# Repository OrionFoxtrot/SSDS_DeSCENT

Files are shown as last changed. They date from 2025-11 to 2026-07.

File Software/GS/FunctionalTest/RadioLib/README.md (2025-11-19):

# RadioLib   

### _One radio library to rule them all!_

## Universal wireless communication library for embedded devices

RadioLib allows its users to integrate all sorts of different wireless communication modules, protocols and even digital modes into a single consistent system.
Want to add a Bluetooth interface to your LoRa network? Sure thing! Do you just want to go really old-school and play around with radio teletype, slow-scan TV, or even Hellschreiber using nothing but a cheap radio module? Why not!

RadioLib natively supports Arduino, but can run in non-Arduino environments as well! See [this Wiki page](https://github.com/jgromes/RadioLib/wiki/Porting-to-non-Arduino-Platforms) and [examples/NonArduino](https://github.com/jgromes/RadioLib/tree/master/examples/NonArduino).

RadioLib was originally created as a driver for [__RadioShield__](https://github.com/jgromes/RadioShield), but it can be used to control as many different wireless modules as you like - or at least as many as your microcontroller can handle!

### Quick links:
* [__Wiki__](https://github.com/jgromes/RadioLib/wiki) - contains useful general information on using this library
* [__FAQ__](https://github.com/jgromes/RadioLib/wiki/Frequently-Asked-Questions) - frequently asked questions, and answers
* [__API Reference__](https://jgromes.github.io/RadioLib) - full API reference, automatically generated from the source code
* [__Status Code Decoder__](https://radiolib-org.github.io/status_decoder/decode.html) - decoder for status codes returned by RadioLib methods
* [__Debug Log Decoder__](https://radiolib-org.github.io/debug_decoder/decode.html) - decoder for RadioLib SPI debug logs

### Supported modules:
* __CC1101__ FSK radio module
* __LLCC68__ LoRa module
* __LR11x0__ series LoRa/GFSK modules (LR1110, LR1120, LR1121)
* __nRF24L01__ 2.4 GHz module
* __RF69__ FSK/OOK radio module
* __RFM2x__ series FSK modules (RFM22, RFM23)
* __RFM9x__ series LoRa modules (RFM95, RFM96, RFM97, RFM98)
* __Si443x__ series FSK modules (Si4430, Si4431, Si4432)
* __STM32WL__ integrated microcontroller/LoRa module
* __SX126x__ series LoRa modules (SX1261, SX1262, SX1268)
* __SX127x__ series LoRa modules (SX1272, SX1273, SX1276, SX1277, SX1278, SX1279)
* __SX128x__ series LoRa/GFSK/BLE/FLRC modules (SX1280, SX1281, SX1282)
* __SX123x__ FSK/OOK radio modules (SX1231, SX1233)

### Supported protocols and digital modes:
* [__AX.25__](https://www.sigidwiki.com/wiki/PACKET) using 2-FSK or AFSK for modules:  
SX127x, RFM9x, SX126x, RF69, SX1231, CC1101, RFM2x, Si443x, LR11x0 and SX128x
* [__RTTY__](https://www.sigidwiki.com/wiki/RTTY) using 2-FSK or AFSK for modules:  
SX127x, RFM9x, SX126x, RF69, SX1231, CC1101, nRF24L01, RFM2x, Si443x, LR11x0 and SX128x
* [__Morse Code__](https://www.sigidwiki.com/wiki/Morse_Code_(CW)) using 2-FSK or AFSK for modules:  
SX127x, RFM9x, SX126x, RF69, SX1231, CC1101, nRF24L01, RFM2x, Si443x, LR11x0 and SX128x
* [__SSTV__](https://www.sigidwiki.com/wiki/SSTV) using 2-FSK or AFSK for modules:  
SX127x, RFM9x, SX126x, RF69, SX1231, CC1101, RFM2x and Si443x
* [__Hellschreiber__](https://www.sigidwiki.com/wiki/Hellschreiber) using 2-FSK or AFSK for modules:  
SX127x, RFM9x, SX126x, RF69, SX1231, CC1101, nRF24L01, RFM2x, Si443x, LR11x0 and SX128x
* [__APRS__](https://www.sigidwiki.com/wiki/APRS) using AFSK for modules:  
SX127x, RFM9x, SX126x, RF69, SX1231, CC1101, nRF24L01, RFM2x, Si443x and SX128x
* [__POCSAG__](https://www.sigidwiki.com/wiki/POCSAG) using 2-FSK for modules:  
SX127x, RFM9x, RF69, SX1231, CC1101, nRF24L01, RFM2x and Si443x
* [__LoRaWAN__](https://lora-alliance.org/) using LoRa and FSK for modules:  
SX127x, RFM9x, SX126x, LR11x0 and SX128x
  * Supports Class A and C (and Multicast over C).
  * Pre-certified for Class A.
  * See the [wiki](https://github.com/jgromes/RadioLib/wiki/LoRaWAN) and [notes](https://github.com/jgromes/RadioLib/blob/master/examples/LoRaWAN/LoRaWAN_Starter/notes.md) for more information.

### Supported Arduino platforms:
* __Arduino__  
  * [__AVR__](https://github.com/arduino/ArduinoCore-avr) - Arduino Uno, Mega, Leonardo, Pro Mini, Nano etc.
    * NOTE: Arduino boards based on ATmega328 (Uno, Pro Mini, Nano etc.) and smaller are NOT recommended. This is because the ATmega328 MCU is very constrained in terms of program and memory size, so the library will end up taking most of the space available. 
  * [__mbed__](https://github.com/arduino/ArduinoCore-mbed) - Arduino Nano 33 BLE and Arduino Portenta H7
  * [__megaAVR__](https://github.com/arduino/ArduinoCore-megaavr) - Arduino Uno WiFi Rev.2 and Nano Every
  * [__SAM__](https://github.com/arduino/ArduinoCore-sam) - Arduino Due
  * [__SAMD__](https://github.com/arduino/ArduinoCore-samd) - Arduino Zero, MKR boards, M0 Pro etc.
  * [__Renesas__](https://github.com/arduino/ArduinoCore-renesas) - Arduino Uno R4

* __Adafruit__
  * [__SAMD__](https://github.com/adafruit/ArduinoCore-samd) - Adafruit Feather M0 and M4 boards (Feather, Metro, Gemma, Trinket etc.)
  * [__nRF52__](https://github.com/adafruit/Adafruit_nRF52_Arduino) - Adafruit Feather nRF528x, Bluefruit and CLUE

* __Espressif__
  * [__ESP32__](https://github.com/espressif/arduino-esp32) - ESP32-based boards
  * [__ESP8266__](https://github.com/esp8266/Arduino) - ESP8266-based boards

* __Intel__
  * [__Curie__](https://github.com/arduino/ArduinoCore-arc32) - Arduino 101

* __SparkFun__
  * [__Apollo3__](https://github.com/sparkfun/Arduino_Apollo3) - Sparkfun Artemis Redboard

* __ST Microelectronics__
  * [__STM32__ (official core)](https://github.com/stm32duino/Arduino_Core_STM32) - STM32 Nucleo, Discovery, Maple, BluePill, BlackPill etc.
  * [__STM32__ (unofficial core)](https://github.com/rogerclarkmelbourne/Arduino_STM32) - STM32F1 and STM32F4-based boards

* __MCUdude__
  * [__MegaCoreX__](https://github.com/MCUdude/MegaCoreX) - megaAVR-0 series (ATmega4809, ATmega3209 etc.)
  * [__MegaCore__](https://github.com/MCUdude/MegaCore) - AVR (ATmega1281, ATmega640 etc.)

* __Raspberry Pi__
  * [__RP2040__ (official core)](https://github.com/arduino/ArduinoCore-mbed) - Raspberry Pi Pico and Arduino Nano RP2040 Connect
  * [__RP2040__ (unofficial core)](https://github.com/earlephilhower/arduino-pico) - Raspberry Pi Pico/RP2040-based boards
  * [__Raspberry Pi__](https://github.com/me-no-dev/RasPiArduino) - Arduino framework for RaspberryPI

* __Heltec__
  * [__CubeCell__](https://github.com/HelTecAutomation/CubeCell-Arduino) - ASR650X series (CubeCell-Board, CubeCell-Capsule, CubeCell-Module etc.)

* __PJRC__
  * [__Teensy__](https://github.com/PaulStoffregen/cores) - Teensy 2.x, 3.x and 4.x boards

* __Silicon Labs__
  * [__EFR32__](https://github.com/SiliconLabs/arduino) - Silicon Labs xG24, xG27 and other boards

The list above is by no means exhaustive - RadioLib code is independent of the used platform! Compilation of all examples is tested for all platforms officially supported prior to releasing new version. In addition, RadioLib includes an internal hardware abstraction layer, which allows it to be easily ported even to non-Arduino environments.

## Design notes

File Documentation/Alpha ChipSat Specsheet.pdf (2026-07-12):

# Flight-proven LEO ChipSat

## Designed for free-flying light sails (Alpha CubeSat mission)

## Applications

### - Low power, long range communications - Remote sensing / distributed sensing - Short-duration multi-day LEO operation - Atmospheric or ground-based sensing - Telemetry for lightweight solar/laser sails

### Dimensions: 58mm x 58mm x 3mm | Mass: 6g

## Capabilities Summary

Power: Wireless operation via 780mW PV (one-sided); Potential modifications: dual-sided solar or battery-only Processing: 16MHz CPU speed; 32KB Flash, 2KB SRAM; Potential modification: external flash memory

## Comms: Semtech SX1276; +20dBm TX; 70cm Band; LoRa, (G)FSK, (G)MSK, and OOK

Position/Attitude determination: GNSS Receiver + 9-DOF IMU (accelerometer, gyroscope, magnetometer)

## Environmental Sensing: Temperature + 3-DOF magnetometer from IMU Structure: Thin flexible polyimide (Kapton) PCB

## Survivability

## Vacuum ☑ | Launch loads/vibration ☑ | Radiation* ⮽ | Terminal-velocity ground impact ☑

Operating temperature: -40°C – +85°C (additional limitations if modified to include energy storage)
*No radiation shielding / rad-hard avionics –recommended for short-term missions w/ large quantities of ChipSats

## Additional Specifications

`

MCU | ATmega328p-AU
I/O Pins: | UART x1, I2C x1, SPI x1, 10-bit ADC x6, GPIO x8 | Sleep current: | 4.4 µA
Clock Speed: | 16MHz | Flash Memory: | 32KB | SRAM: | 2KB | EEPROM: | 1KB
Sensors | STS21 Temperature Sensor | LSM9DS1 9-DOF IMU
Temp | Accel | Gyro | Mag
Resolution: | 0.08°C | 0.732 mg | 0.875 dps | 0.014 µT
Range: | -40° - 125°C | ± 16g | ± 245 dps | ±400 µT
GPS | SkyTraq Orion B16-01; L1 GPS/Galileo/GLONASS/BeiDou/QZSS; Space-rated
Accuracy: | Position: | 2m | Velocity: | 0.1m/s | Time: | 5ns | TTFF: | 1 min
Power | L6920 regulator IC + 780mW GaAs PV | No energy storage onboard
Lifespan | Indefinite operation under solar illumination (dependent on sun-orientation)
Comms | SX1276 (built into HopeRF RFM96W); also capable of (G)FSK, (G)MSK, OOK
Freq: | 433MHz | BW: | 7.8 - 500KHz | TX PWR: | +20dBm | Modulation: | LoRa
Approx. Range: | (w/ below receiver equipment) | 50km | LEO | GEO | Cislunar
Estimated LoRa Data rate (bps): | | Low-gain omni | 488 bps | 146 bps | X | X
| | High-gain Yagi | 3.5 kbps | 488 bps | 45 bps | X
| | Large parabolic dish | 22 kbps | 3.5 kbps | 146 bps | 11 bps

## ChipSat layout

### ChipSat architecture

For more information:
✉ mp336@cornell.edu spacecraftresearch.com

Est. cost (per ChipSat):

## $1300 USD (Orbital) / $200 USD (Terrestrial)

# ChipSat V5 (2022-2025)

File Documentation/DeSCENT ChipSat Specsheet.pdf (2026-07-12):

## Compact ChipSat with solar battery charging

## Designed for suborbital rocket deployment and atmospheric data collection (DeSCENT mission)

## Applications

## - Low power, long range communications - Remote sensing / distributed sensing - Short-duration multi-day LEO operation - Atmospheric or ground-based sensing

## Dimensions: 60mm x 50mm x 4.5mm | Mass: 20g

## Capabilities Summary

Power: Wireless self-sustaining operation via dual 300mW PV (one per side) + 300mAh LiPo battery Processing: 32-bit ARM Cortex-M4; 48MHz; 256KB Flash, 65KB SRAM; 2MB external flash memory

## Comms: Semtech SX126x; +22dBm TX; 915MHz ISM Band; LoRa, (G)FSK, (G)MSK, and BPSK

Position/Attitude determination: GNSS Receiver + 9-DOF IMU (accelerometer, gyroscope, magnetometer) Environmental Sensing: Temperature, pressure, and humidity sensors; 3-DOF magnetometer from IMU

## Survivability

## Vacuum ☑ | Launch loads/vibration ☑ | Radiation* ⮽ | Terminal-velocity ground impact ☑

Operating temperature: -10°C – +60°C with LiPo battery | -40°C – +85°C with solar-only configuration
*No radiation shielding / rad-hard avionics –recommended for short-term missions w/ large quantities of ChipSats

## Additional Specifications

MCU | Seeed Studio Wio-E5 (STM32WLE5 32-bit ARM Cortex M4) + W25Q16 Ext Flash
I/O Pins: | UART x3, I2C x1, SPI x1, 12-bit ADC x1, GPIO x6 | Sleep current: | 2.1 µA
Clock Speed: | 48MHz | Flash Memory: | 256KB | SRAM: | 65KB | Ext. Flash: | 2MB
Sensors | BME280 Environmental | BNO085 9-DOF IMU
Temp | Pressure | Humidity | Accel | Gyro | Mag
Accuracy: | 1°C | 1.0 hPa | 3% RH | 0.3m/s² | 3.1 dps | 1.4 µT
Range: | -40°-85°C | 300-1100 hPa | 0-100% | ± 8g | ± 2000 dps | ±800 µT
GPS | u-blox MAX M10S; L1 GPS/Galileo/GLONASS/BeiDou; NOTE: CoCom Limits
Accuracy: | 2m | TTFF: | 2 min | Max alt: | 80km | Max vel: | 500m/s
Power | BQ25570 regulator IC + 300mAh LiPo Batt + 300mW GaAs PV
Batt. Life: | 10hr battery-only operation w/ frequent radio TX | Indefinite w/ solar charging
Comms | SX126x (built into Wio-E5 MCU); also capable of (G)FSK, (G)MSK, and BPSK
Freq: | 915MHz | BW: | 62.5 - 500KHz | TX PWR: | +22dBm | Modulation: | LoRa
Approx. Range: | (w/ below receiver equipment) | 50km | LEO | GEO | Cislunar
Estimated LoRa Data rate (bps): *requires hardware change | | Low-gain omni | 488 bps | 91 bps | X | X
| | High-gain Yagi | 3.5 kbps | 268 bps | 36 bps* | X
| | Large parabolic dish | 22 kbps | 1.9 kbps | 91 bps | 11 bps*

# ChipSat V6 (2023-2026)

## ChipSat layout

## ChipSat architecture

For more information:

### ✉ mp336@cornell.edu spacecraftresearch.com

Est. cost:

## $200 USD

per ChipSat

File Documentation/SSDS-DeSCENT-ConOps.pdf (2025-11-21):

# Concept of Operations (ConOps) – DeSCENT Mission

## 1 1. Mission Overview

The Demonstration of Suborbital ChipSats Ejected from New Shepard Test Flight (DeSCENT) is a Cornell SSDS mission in collaboration with Johns Hopkins APL.

The mission will deploy 100 ChipSats from a Blue Origin New Shepard suborbital launch vehicle at ~100 km altitude.

## 1.1 Primary objectives:

Goal 1 The mission shall collect in-situ sensor data from a distributed fleet of chipsats.

Goal 1.1 The mission shall collect data that demonstrates the potential of chipsats for atmospheric science. [Goal 1]

Goal 2 The mission shall characterize the free-fall dispersion dynamics and the landing ellipse of a chipsat fleet.

## 2 Mission Phases

## 2.1 Pre-Launch Integration

The DeSCENT payload consists of a spring-loaded deployer containing 100 ChipSats, integrated alongside other experiments within the APL JANUS platform for the New Shepard propulsion Module (PM).

ChipSats remain powered off inside the deployer until ejection, per safety requirements.

Payload is mounted within an AxBxC mm envelope, inverted relative to vehicle axes.

## 2.2 Launch & Ascent

New Shepard PM launches vertically from Blue Origin’s West Texas Launch Site.

The BE-3 engine burns for ~2.5 minutes, propelling the vehicle and payload stack above 100 km altitude.

ChipSats remain stowed; environmental loads are verified against payload specifications.

## 2.3 Apogee & Deployment

At apogee (~100 km, ~T+3 min), a burn-wire mechanism triggers deployer springs, releasing ChipSats at ~0.2–0.4 m/s relative velocity.

Doors hinge open, ejecting ChipSats into free space.

Deployment is vertical relative to launch orientation, ensuring controlled dispersion.

## 2.4 Free-Fall Descent

Each ChipSat (~20 g, <50×50×4 mm) enters a ballistic free-fall trajectory, reaching terminal velocities between ~110–220 m/s.

Onboard sensors (BME280, BNO085 IMU, GNSS) continuously log data.

Communications strategy:

- Low-density, real-time telemetry sent to ground station.
- High-density data stored in onboard flash retrievable upon recovery.

## 2.5 Impact & Recovery

ChipSats are designed to survive terminal impact due to their low mass and high structural frequencies.

GNSS beacons and LoRa transmissions support localization.

Ground recovery teams search the landing ellipse to collect ChipSats.

## 2.6 Post-Mission Analysis

Recovered ChipSats provide stored high-fidelity datasets.

Combined telemetry and flash data validate free-fall models, atmospheric measurements, and swarm dispersion behavior.

Results inform future ChipSat swarms for atmospheric entry on Earth or other planetary bodies.

## 3 Key Systems

Deployer: Aluminum structure with spring-loaded ejection bars and burn-wire trigger.

ChipSat Command and Data Handling: MCU/LoRa IC, Environmental sensors (BME280), IMU (BNO085), GNSS, Flash storage.

ChipSat Communications: LoRa at 915 MHz ISM band, asynchronous chirp spread spectrum modulation.

ChipSat Power: Solar and 350 mAh LiPo, low-duty cycle operation.

Integration Platform: APL’s JANUS system, providing power control, data monitoring, and environmental characterization.

## 4 Operational Constraints

Must meet Blue Origin payload integration requirements: mechanical envelope, EMI/EMC, vibration, and thermal testing.

Deployer must pose no risk to launch vehicle, other payloads, or personnel.

RF transmissions must not interfere with New Shepard telemetry.

Recovery probability and data survival are mission-critical success metrics.

## 5 Success Criteria (MIS Requirements)

MIS 1 One hundred chipsats shall be deployed from the New Shepard suborbital launch vehicle at approximately 100 km apogee.

MIS 2 The chipsat sensor data shall be collected from chipsat descent trajectories and landing positions.

MIS 2.1 The collected chipsat data shall contain in-situ atmospheric sensor data and measurements of chipsat free-fall kinematics. [MIS 2]

MIS 3 Two percent of chipsats shall survive terminal velocity impact with the ground.

MIS 4 X percent of chipsats shall be recovered after landing.

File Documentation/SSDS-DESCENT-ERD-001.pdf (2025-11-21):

Effective Date: September 9th, 2025 Revision: 0

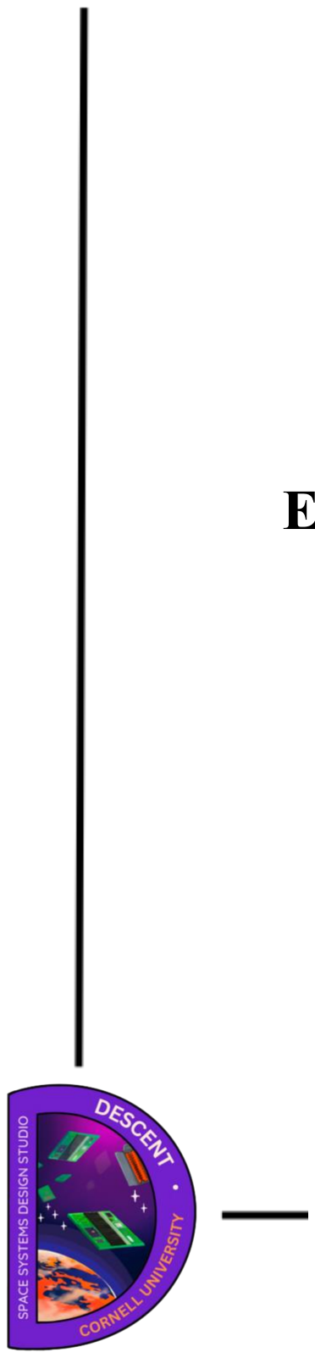
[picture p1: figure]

Check the DESCENT Box Folder at this URL (https://cornell.app.box.com/folder/213553157379?s=2hq835s9t41mr3z1efjbw8ddljec1i8f) to verify that this is the correct version prior to use.

## DESCENT SSDS-DESCENT-ERD-001

# DESCENT Engineering Requirements Document (ERD)

School of Mechanical & Aerospace Engineering Ithaca, New York

DESCENT Engineering Requirements Document (ERD) | SSDS-DESCENT-ERD-001
| Revision: 0

## DESCENT Engineering Requirements Document (ERD)

DESCENT Electronic Signature Page

Prepared By:

Mark Lohatepanont, Josh Umansky-Castro, Richard Zheng, Arthur Chadwick

Approved By:

__________________
____________________________________________

School of Mechanical & Aerospace Engineering Ithaca, New York

Revision: 0

## Preface

This is the Engineering Requirements Document (ERD) to be shared with relevant stakeholders on the DESCENT project. The ERD shows the requirements necessary for the mission, safety, deployer, chipsat, power, communications, command and data handling, mechanical, and environmental requirements.

Any questions should be addressed to:

Mark Lohatepanont
Cornell University PhD Student DESCENT project
ml2828@cornell.edu
Ithaca, NY 14850

Revision: 0

## Change History Log

Revision | Effective Date | Description of Changes | Sections Affected
0 | Sept. 9th, 2025 | Document formatting created based on NASA example[7] (https://www.nesdis.noaa.gov/s3/2022-03/474-00002-01_JPSS-CIS-ICD-Vol-I-_External_0124E.pdf) . Table of Contents outline created. Initial requirements transcribed from DESCENT requirements meeting. | All

Revision: 0

Revision: 0

### 0 What is an ERD?

An Engineering Requirements Document (ERD) is a collection of information that shares the “shall” statements, or the requirements, of a project. Engineers use these requirements to determine the scope of the design. An ERD may take other forms as well. Some examples of a technical requirements document used by NASA are a System Requirements Document (SRD), Project Requirements Document (PRD), Interface Requirements Document (IRD), and a Software Requirements Specification (SRS)[1] (https://www.nasa.gov/reference/4-2-technical-requirements-definition/)

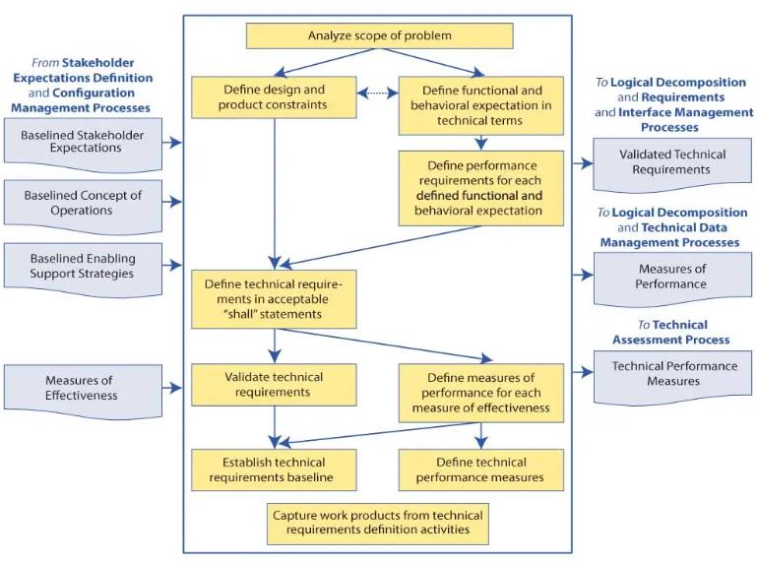
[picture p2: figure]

Figure: Technical Requirements Definition Process[1] (https://www.nasa.gov/reference/4-2-technical-requirements-definition/) .

Defining requirements connects the vision of the product or mission between stakeholders like the project managers, engineers, and customers; on the left side of the diagram above, we see those inputs mentioned. In the middle section, it outlines important actions in the process like defining constraints, functional vs performance requirements, and validation techniques. A requirement is as good as its applicability and validity. Measures of Performance (MOPs) and Technical Performance Measures (TPMs) are the measurable numbers in the requirements[1] (https://www.nasa.gov/reference/4-2-technical-requirements-definition/)

Revision: 0

### 0.1 Acronyms

APL | Applied Physics Laboratory
ADCS | Attitude Dynamics & Control Subsystem / Attitude Control System
CDH | Command and Data Handling
CONOPs | Concept of Operations
DPLY | Deployer
ERD | Engineering Requirements Document
ESD | Electrostatic Discharge
FCC | Federal Communications Commission
FMEA | Failure Modes & Effects Analysis
FMSA | Fault Management & System Autonomy
GPS | Global Positioning System
I&T | Integration & Test
INT | Integration
LV / LVA | Launch Vehicle
MIS | Mission
MIL-STD | Military Standard
MPP | Maximum Power Point
NASA | National Aeronautics Space Administration
NIR | Near Infrared Light
NTSS | NASA Technical Standards System
NTSP | NASA Technical Standards Program
OCE | Office of the NASA Chief Engineer
PCB | Printed Circuit Board
PLD | Payload
PWR | Power Subsystem / Power System / Electrical Power System
RF | Radio Frequency
SE | Space Environment
SSDS | Space Systems Design Studio
T&C | Telemetry & Command / Command & Data Handling
TBC | To Be Confirmed
TBD | To Be Determined
TCS | Thermal Control Subsystem / Thermal System
TPM | Technical Performance Measure
TRL | Technical Readiness Level
TTFF | Time to First Fix
FM | Fault Management

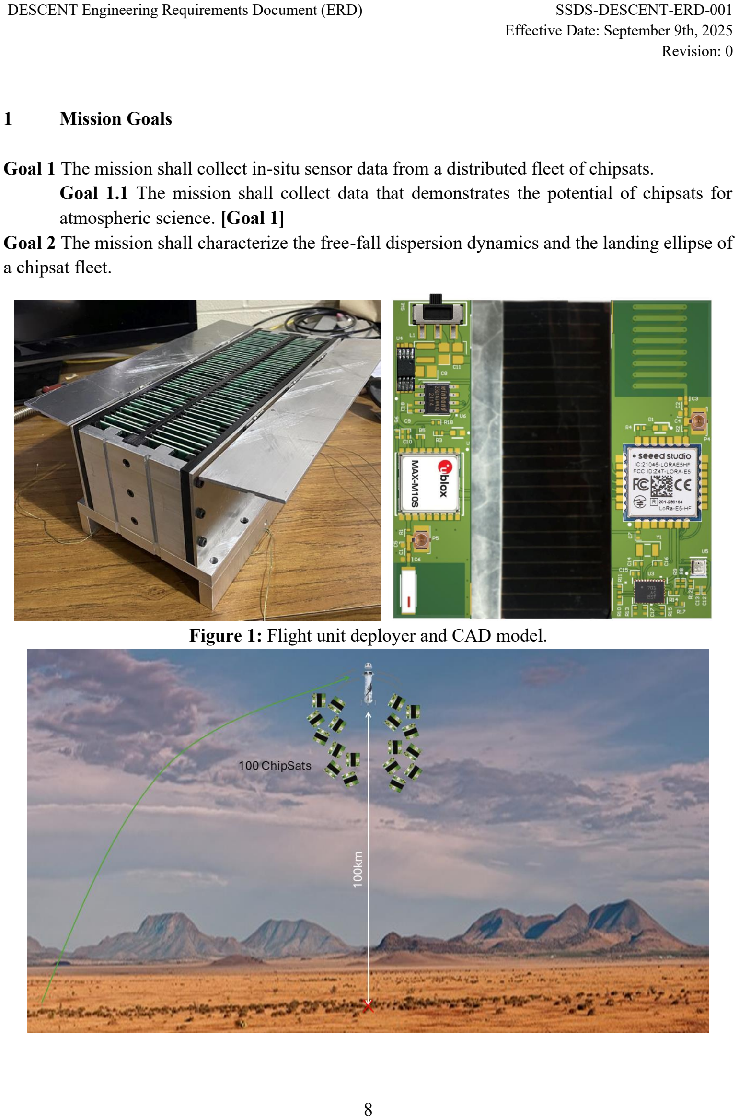
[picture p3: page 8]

Revision: 0

### 1 Mission Goals

Goal 1 The mission shall collect in-situ sensor data from a distributed fleet of chipsats.
Goal 1.1 The mission shall collect data that demonstrates the potential of chipsats for atmospheric science. [Goal 1]
Goal 2 The mission shall characterize the free-fall dispersion dynamics and the landing ellipse of a chipsat fleet.

Figure 1: Flight unit deployer and CAD model.

Revision: 0

Figure 2: Demonstration of Suborbital ChipSats Ejected from New Shepard Test Flight (DeSCENT).

Revision: 0

### 2 Mission-Level Requirements

MIS 1 One hundred chipsats shall be deployed from the New Shepard suborbital launch vehicle at approximately 100 km apogee.
MIS 2 The chipsat sensor data shall be collected from chipsat descent trajectories and landing positions.
MIS 2.1 The collected chipsat data shall contain in-situ atmospheric sensor data and measurements of chipsat free-fall kinematics. [MIS 2]
MIS 3 Two percent of chipsats shall survive terminal velocity impact with the ground.
MIS 4 X percent of chipsats shall be recovered after landing.

### 3 Safety Requirements

FM 1 The chipsat shall be powered off when stowed in the deployer. [MIS 4]
FM 2 The chipsat shall have X mAh capacity. [MIS 4]
FM 3 The chipsat RF transmissions shall not interfere with the New Shepard launch vehicle. [MIS 4]
FM 3.1 The chipsat RF transmit power (TX) and frequency shall not interfere with the New Shepard launch vehicle. [FM 3]
FM 4 The chipsat shall weigh < X g. [MIS 4]
FM 5 The mechanical deployer shall remain in-tact and attached to the rocket. [MIS 4]
FM 6 The burn-wire shall not disrupt operations. [MIS 4]
FM 7 The chipsat deployer shall cause no harm to the vehicle, payloads, or personnel. [Blue Origin, APL]
FM 7.1 The chipsat deployer shall cause no harm to Blue Origin’s Propulsion Module. [FM 7]
FM 7.2 The chipsat deployer shall cause no harm to Blue Origin’s Crew Capsule. [FM 7] The chipsat deployer shall cause no harm to John Hopkins’ APL JANUS payload. [FM 7] FM 7.3 The chipsat deployer shall cause no harm to other payloads. [FM 7]
FM 7.4 The chipsat deployer shall cause no harm to Blue Origin personnel. [FM 7]

### 4 Deployment Requirements

DPLY 1 The deployer shall automatically deploy at apogee. [MIS 2]
DPLY 1.1 The deployer shall deploy during APL pulsed signal. [DPLY 1] DPLY 1.2 The deployer shall deploy between two to four minutes. [DPLY 1] DPLY 2 The deployer shall deploy vertically from NS Launch. [MIS 2]

Revision: 0

DPLY 3 The deployer shall deploy chipsats at 0.2 to 0.4 m/s. [MIS 4]
DPLY 4 The deployer shall interface using a MIL-STD D-Sub connector to APL’s JANUS payload. [MIS 4]
DPLY 5 The deployer shall be bounded by X volume. [MIS 4]
DPLY 6 The deployer shall weigh less than 50 lbs (10 kg).
DPLY 7 The deployer shall survive the launch and launch environment. DPLY 8 The deployer shall deploy at -46 degrees Celsius.
DPLY 9 The deployer shall house and deploy 100 chipsats.
DPLY 10 The deployer shall be mounted to the APL JANUS plate.
DPLY 11 The deployer shall adhere to the Blue Origin Propulsion Module User’s Guide.
DPLY 12 The deployer slots shall house chipsats of size | X | m, | X | m, | X | m.
DPLY 13 The deployer shall have the capability to be stowed for 3 months.

### 5 Chipsat Requirements

### 5.1 Power Requirements

PWR 1 The chipsat shall remain off when stowed in the deployer and turn on upon deployment PWR 1.1 The chipsat shall have a snap action lever switch to activate the circuit upon deployment. [PWR 1, MECH X]
PWR 1.2 The chipsat batteries shall be fully charged when stowed before launch.
PWR 2 The chipsat shall remain on during descent and recovery. [MIS 1, MIS 2]
PWR 2.1 The chipsat shall remain powered on via solar during extended recovery. [PWR 2]
PWR 2.1.1 The chipsat maximum power draw shall not continuously, for 1 hour, bleed MPP of solar cell @ 300 mA @ 1.1V. [PWR 2.1]
PWR 2.1.2 The chipsat solar panel shall be able to recharge the battery. [PWR 2.1] PWR 2.2 The chipsat battery capacity shall be sufficient for X hours of operation. [PWR 2]
PWR 2.3 The chipsat battery shall be used to store energy during descent and short term recovery. [PWR 2]

### 5.2 Communications Requirements

COMMS 1 The chipsat shall communicate across descent and recovery.
COMMS 1.1 The chipsat ground communications link shall be maintained across the longest distance at Propulsion Module apogee. [COMMS 1]
COMMS 2 The chipsat TX power shall remain within maximum power draw of the power source.

Revision: 0

COMMS 3 The chipsat communications shall be maintained via commercially available, low power, and long range chips.
COMMS 3.1 The chipsat communications shall use a 915 mHz Lora chip. [COMMS 3] COMMS 4 The chipsat communications shall begin when each chipsat leaves the deployer. COMMS 5 The chipsats shall stop transmitting on command. [MIS 4]
COMMS 6 The chipsat communications shall transmit at 0.1 Hz during the descent phase.
COMMS 7 The chipsat shall transmit at | X | Hz (once every 10-20 sec) when in ground recovery
phase.
COMMS 8 The chipsat communications antenna shall fit within the mechanical envelope. [MECH 3.X]
COMMS 8.1 The chipsat communications antenna shall be a helical PCB.

### 5.3 Command & Data Handling

CDH 1 Data acquisition shall start after the chipsats leave the deployer.
CDH 2 All sensors shall sample at > 1 Hz during descent.
CDH 3 The chipsat shall collect internal and external data.
CDH 3.1 The chipsat shall collect humidity, temperature, pressure. [CDH 3]
CDH 3.2 The chipsat shall collect linear acceleration, angular velocity, and magnetic field vector data. [CDH 3]
CDH 3.3 The chipsat shall collect GPS position data. [CDH 3]
CDH 3.4 The chipsat shall carry the BME280. [CDH 3]
CDH 3.5 The chipsat shall carry the BNO085. [CDH 3]
CDH 3.6 The chipsat shall carry the UBloxMax 10s-00B. [CDH 3]
CDH 4 All sensors shall sample at | X | Hz (once every 10-20 sec) during ground recovery phase,
with GPS exception.
CDH 5 The chipsat shall log all collected sensor data.
CDH 6 The GPS module Time to First Fix (TTFF) shall be less than 3 minutes.

### 5.4 Mechanical Requirements

MECH 1 The chipsat shall fit within the deployer.
MECH 1.1 The chipsat shall be less than X mm, X mm, X mm. in volume. [MECH 1] MECH 2 The chipsat shall be less than X ballistic coefficient.
MECH 3 The chipsat shall survive deployment and terminal velocity impact with the ground. MECH 3.1 The chipsat shall be manufactured from a rigid PCB substrate. [MECH 3] MECH 3.1.1 The chipsat shall be made from FR-9. [MECH 3.1]

Revision: 0

MECH 3.1.2 The chipsat 1.6 mm FRCI shall be used to improve communications and performance. [MECH 3.1]
MECH 3.2 The chipsat components shall fit within 3 mm of the face of the PCB. [MECH 3]
MECH 3.3 The chipsat components shall extend off the edge of the PCB. [MECH 3] MECH 3.4 All components shall be strongly adhere to the PCB. [MECH 3]
MECH 3.4.1 All electrical components shall be high strength mounted with solder or additionally bonded with adhesive when needed. [MECH 3.4]
MECH 4 The chipsat switch shall be fully depressed while in the deployer.
MECH 4.1 The chipsat shall fit snuggly within the deployer. [MECH 4]
MECH 5 The chipsat shall be mass manufacturable.
MECH 5.1 The chipsat shall have > 90% automated manufacturing process. [MECH 5]

### 5.5 Environmental Requirements

ENV 1 The chipsat shall operate in temperatures ranging from -50 to 85 degrees Celsius.
ENV 2 The chipsat shall operate in a vacuum.
ENV 3 The chipsat shall survive X months of storage in the deployer at temperatures ranging from 0 to 40 degrees Celsius.
ENV 4 The deployed chipsat shall survive 48 hours outside the deployer after landing.
ENV 4.1 The chipsat shall survive 12 hours of direct sunlight.

### 6 Ground Station Requirements

### 6.1 Power Requirements

PWR 1 The forward ground terminal shall contain | X | mAh LiPo battery with energy enough to
operate for more than | 6 | hours in deployed field mode without external power.
PWR 2 The forward ground terminal shall support standby for more than 6 hours with autonomous wake on reception or schedule.

### 6.2 Comms Requirements

COMS 1 The forward ground terminal shall receive complete LoRa packets from a chipsat at ranges up to X km line-of-sight at NS apogee geometry, with link margin ≥ 10 dB under clear-sky conditions.
COMS 2 The system shall operate in the LoRa 915 MHz band.

Revision: 0

COMS 3 The forward ground terminal shall use a directional antenna (e.g., Yagi/patch) with
boresight | gain | more | than | X | dBi.
COMS 4 The forward ground terminal receiver sensitivity shall be better than | X.
COMS | 5 | The | RF | front-end | shall | include | SAW/BPF | filtering.
COMS 6 The ground segment shall support simultaneous reception of more than | X | concurrent
chipsats.
COMS 7 Antenna pointing error shall be within | X | degrees; for fixed stations, set-and-hold
alignment | | | tolerance | | within | | Y | degrees.
COMS 8 The system shall decode and forward and log 100% of valid CRC packets received above sensitivity.

### 6.3 Mechanical

MECH 1 The forward ground terminal shall have a packed mass less than X kg and packed volume
within | | | | | Y | | | L.
MECH 2 The forward ground terminal shall be deployable by one person with no tools in ≤ 10 min.
MECH 3 The antenna mount shall withstand gusts to X m/s.

### 6.4 Environmental

ENV 1 forward ground terminal shall be able to operate in 0 to 50 degrees Celsius. ENV 2 forward ground terminal electronics enclosures shall be IP54.

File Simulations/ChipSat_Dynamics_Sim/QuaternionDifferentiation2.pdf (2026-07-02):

Quaternion differentiation

Quaternion differentiation’s formula connects time derivative of component of quaternion q(t) with component of vector of angular velocity W(t). Quaternion q(t)=(q0(t), q1(t), q2(t), q3(t)) determines attitude of rigid body moving with one fixed point, vector of angular velocity W(t)=( Wx(t), Wy(t), Wz(t)) determines angular velocity of this body at point of time t. point of time. Norm of quaternion q(t) is unit, i.e.

( ) | ( ) | ( ) | ( ) 1 ²
3

2
2

2
1

2

q0 t + q t + q t + q t =

(1)

Vector W(t) can be represented as quaternion with zero scalar part, i.e

W (t) (0,W (t),W (t),W (t)) = | x | y | z
(2)

Quaternion differentiation’s formula can be represented as

( ) ( ) 2

( ) 1W t q t
dt

dq t =

(3)

Using quaternion multiplication rule

( ( ) ( ) | ( ) ( ) | ( ) ( )) 2

( ) 1

( ( ) ( ) | ( ) ( ) | ( ) ( )) 2

( ) 1

( ( ) ( ) | ( ) ( ) | ( ) ( )) 2

( ) 1

( ( ) ( ) | ( ) ( ) | ( ) ( )) 2
( ) | 1
0 | 2 | 1

3

0 | 1 | 3

2

0 | 3 | 2

1

1 | 2 | 3

0

W t q t W t q t W t q t
dt

dq t

W t q t W t q t W t q t
dt

dq t

W t q t W t q t W t q t
dt

dq t

W t q t W t q t W t q t
dt

dq t

z | x | y
y | z | x
x | y | z
x | y | z
= | + | −
= | + | −
= | + | −
= − | + | +

(4)

Below formula (3) brief and vigorous derivation follows.

Let R0 is any given vector (quaternion with zero scalar part) fixed in rigid body at initial moment of time t0, Rt is the same vector (quaternion) at moment of time t. Then, obviously

( ) | ( ) ¹
0 R | q t R q t t

− =
(5)

If we differentiate (5) then

dt

dq t R q t q t R
dt

dq t
dt
dRt | ( ) ( ) | ( ) ( ) | 1

0

1
0

−
− = | +

(6)

From (5) and (6) we have

dt

dq t
q t R R q t
dt

dq t
dt
dR | t | t
t | ( ) ( ) | ( ) ( ) | 1
1

−
− = | +

(7)

Because norm of quaternion q(t) is unit, i.e.

( ) ( ) 1 ¹ = ⁻ q t q t
(8)

we have
0 ( ) ( ) | ( ) ( ) | 1
1 | + | =

−
−
dt

dq t
q t q t
dt

dq t

(9)

It follows from (7) and (9) that
( ) ( ) ( ) ( ) 1 | 1
q t
dt

dq t
q t R R
dt

dq t
dt
dR | t | t
t | − | − = | −

(10)

Let

( ) ( ) ( ) | 1
q t
dt

dq t
p t | − =

(11)

Obviously

( ) | ( | ( )) | ( | ( )) | ( ) ( ( ), ( ), ( )) 0 | 1 | 2 | 2
1 | 1 | 1
q t = S q t +V q t = q t − q t q t q t ⁻ | − | −
(12)
where S() =scalar part, V()=vector part of quaternion

Scalar part S(p(t)) of quaternion p(t) equals
0 ( ) | ( ) | ( ) | ( ) ( ( )) | 3
3
2

2
1

1
0
0 = | + | + | + | q = dt

dq t
q dt

dq t
q dt

dq t
q dt

dq t S p t

because norm of quaternion q(t) is unit.

It follows that p(t) is vector. Because Rt is also vector

( ) | ( ) 2[ ( ) ] t | t | Rt p t R − R p t = p t
(13)
where [ab]= cross-product of vector a and vector b.

On the other hand, variable dt dRt is velocity of point of rigid body with one fixed point. Hence

[ ( ) ]t

t W t R
dt

dR =

(14).

Because Rt is arbitrary vector, it follows from (10), (11), (13) and (14)

( ) ( ) ( ) 2 ( ) 2 | 1
q t
dt
dq t W t | p t | − = | =

(15)

It follows from (15) finally that

( ) ( ) 2

( ) 1W t q t
dt

dq t =

(3)

It is necessary to draw attention: in formula (3) angular velocity vector W(t)=(WX(t), WY(t), WZ(t)) is represented by projections on axes of unmoving system of coordinates. If we apply the projections on axes of moving system of coordinates for the same angular velocity vector then obviously:
(0, | ( ), | ( ), | ( )) | ( )(0, ( ), ( ), ( )) ( ) ¹ W t W t W t | q t | W t W t W t q t X | Y | Z | x | y | z

− =
(16)
Where Wx(t), Wy(t), Wz(t) are projections of angular velocity vector on axes of moving system of coordinates.
It follows from (3) and (16) that

( ) ( ( ), ( ), ( ))

( ) ( ) 2

( ) 1
W t W t W t W t q t W t
dt

dq t

= x | y | z

=

(17)
Finally, consider example of formulas (3) and (17) using for so-called conic moving. In this case quaternion q(t) equals:

( sin( ),cos( ),0)) 2 (0, sin ( )

(cos( ),sin( ),0)) 2 , sin

2 ( ) (cos

(cos( ),sin( ),0)) 2 ,sin

2 ( ) (cos

1

t t
dt

dq t

q t | t | t
q t | t | t
ω | ω β ω
ω | ω β | β
ω | ω β | β

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
⎛ ⎟ −
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
(18)

Accordingly (3) and (17) projections of angular velocity vector on axes of unmoving and moving systems of coordinates equals:

( | sin( )sin( ), sin( ) cos( ), (cos( ) 1)) ( ) ( ( ), | ( ), ( )) 2 | ( )
( ) ( | sin( )sin( ), sin( ) cos( ), (1 cos( ))) ( ) ( | ( ), | ( ), | ( )) 2

1

1

= | = − | −
= | = − | −

−

−

ω β | ω ω β | ω ω | β
ω β | ω ω β | ω ω | β
| t | t
dt
dq t W t W t W t | q | t
q t | t | t
dt

dq t W t W t W t

x | y | z
X | Y | Z

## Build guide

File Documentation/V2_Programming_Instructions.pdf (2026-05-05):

# V2 ChipSat Programming Guide

Mark (ml2828), Bryan (bmp85) - Space Systems Design Studio (SSDS)

November 11, 2025

## 1 Required Hardware/Software

V2 ChipSats use the STM32WL and are functionally just STM32 boards. The following lists the required hardware and software.

Hardware:

1. DeSCENT V2.X.X ChipSat
2. Pogo Programmer
3. ST-Link V2
4. Binder Clip (Optional)

Software

1. Arduino IDE
2. STM32CubeProgrammer (https://www.st.com/en/development-tools/stm32cubeprog.html)
3. STM32 Arduino Core Documentation (https://github.com/stm32duino)

## 2 Software Installation Steps

1. Install STM32CubeProgrammer
2. Install STM32 Support in Arduino IDE
(a) Open Arduino IDE and go to File → Preferences.
(b) In Additional Board Manager URLs, add: https://github.com/stm32duino/BoardManagerFiles/raw/main/package_stmicroelectronics_index.json (https://github.com/stm32duino/BoardManagerFiles/raw/main/package_stmicroelectronics_index.json)
(c) Open Tools → Board → Boards Manager.
(d) Search for STM32 MCU based boards and install it.
3. Wire ST-LINK to the Pogo Programmer

The Pogo Programmer has five pins on the right hand side populated with vertical header pins. Each are named accordingly.

ST-LINK Pin | Pogo Programmer Pin
SWDIO SWCLK GND 3.3V NRST | SWDIO SWCLK GND 3.3V NRST

There are some special conditions to connecting the NRST Pin that depend on the color of your ST-Link programmer. SSDS stocks two versions of the ST-Link Programmer, a Black and a Green Version. For the Black Version the Pogo Programmer NRST pin must be jumped to the ST-Link V2’s RST pin for generally use (Post RDP reset). The Green Version can have the Pogo Programmer NRST pin left floating (Post RDP reset).

## 3 Configure Arduino IDE for STM32

- Board: LoRa Boards
- Part Number: LoRa-E5 mini
- Upload Method: STM32CubeProgrammer (SWD)

Generally, you can now upload sketches to the Wio now and skip directly to step 5. However, if your Wio is a newly shipped version and has never been programmed before, you must do the next step to ensure the data protection on the Wio is turned off before you are able to program it.

## 4 Connecting via STM32CubeProgrammer

1. Boot up STM32CubeViewer
2. Plug ST-Link in
3. Click connect on STM32CubeViewer
4. You probably get an error saying it doesn’t exist:

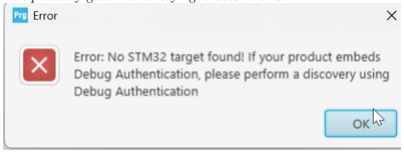
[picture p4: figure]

5. Take the NRST pin on the chipsat and short it to ground
6. Press Connect Again
7. You probably get an error saying something about not being able to read something:

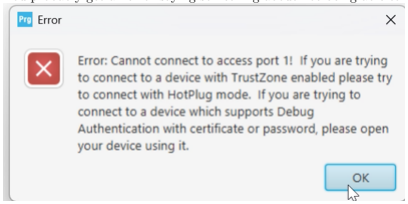
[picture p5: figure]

8. Unplug NRST and leave it open
9. Press Connect Again

10. You probably get an error saying “Error: data read failed”

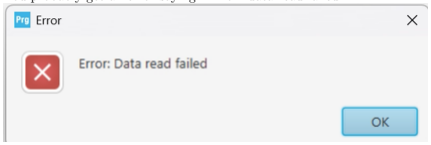
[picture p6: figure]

11. Go to the LHS and press OB (option bytes)
12. Change RDP to AA from BB
13. Press Apply
14. Now it works.

## 5 Uploading a test sketch

1. Open a basic example such as Blink.
2. Click Upload.
3. The sketch will compile and be uploaded via ST-LINK.

## 6 Codebase

Once you can get a blink sketch working, you can check our Github which includes functionality test’s for the chipsat: SSDS V1-V2 (https://github.com/OrionFoxtrot/SSDS_V1-V2_Test_Scripts/tree/main)

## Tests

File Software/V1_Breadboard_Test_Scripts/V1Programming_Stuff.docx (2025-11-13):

Programming pins is SPI

TX/RX for seriall pins

Use 5v

Connect Arduino

Open ArduinoISP

Burn bootloader , Arduino as isp

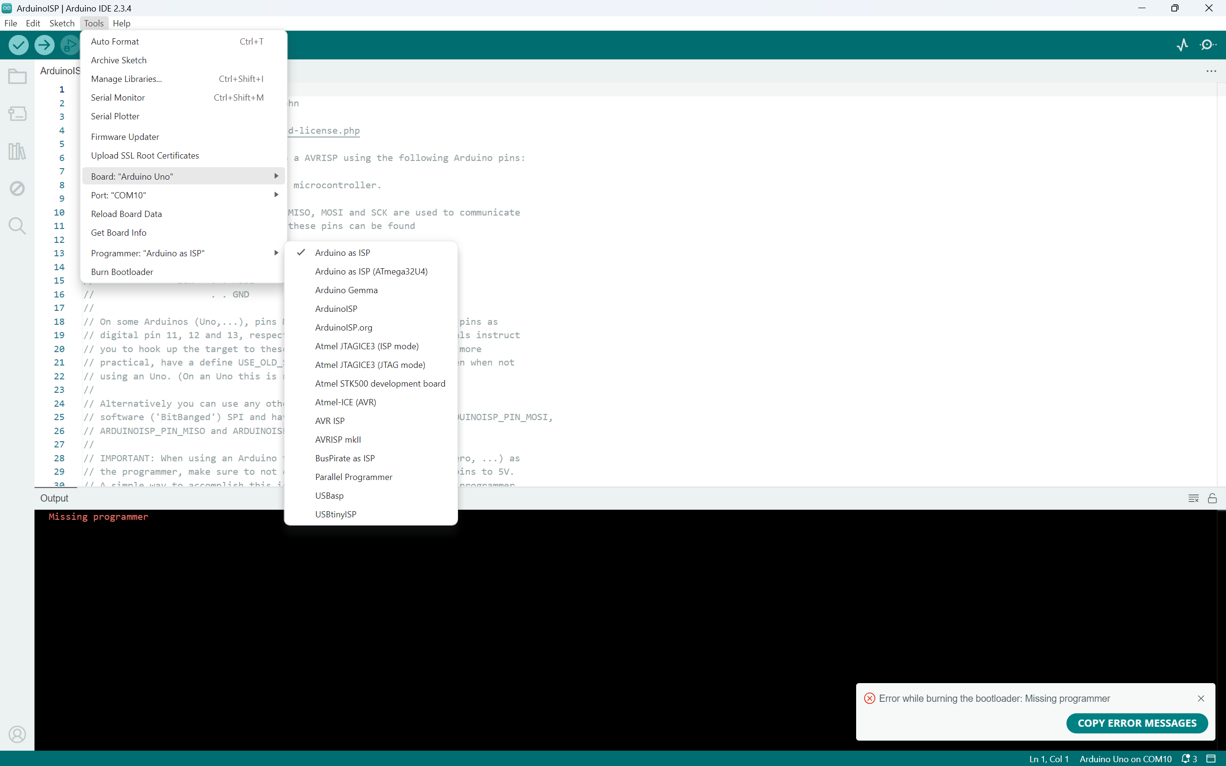
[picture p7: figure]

Then upload using programmer for rcode

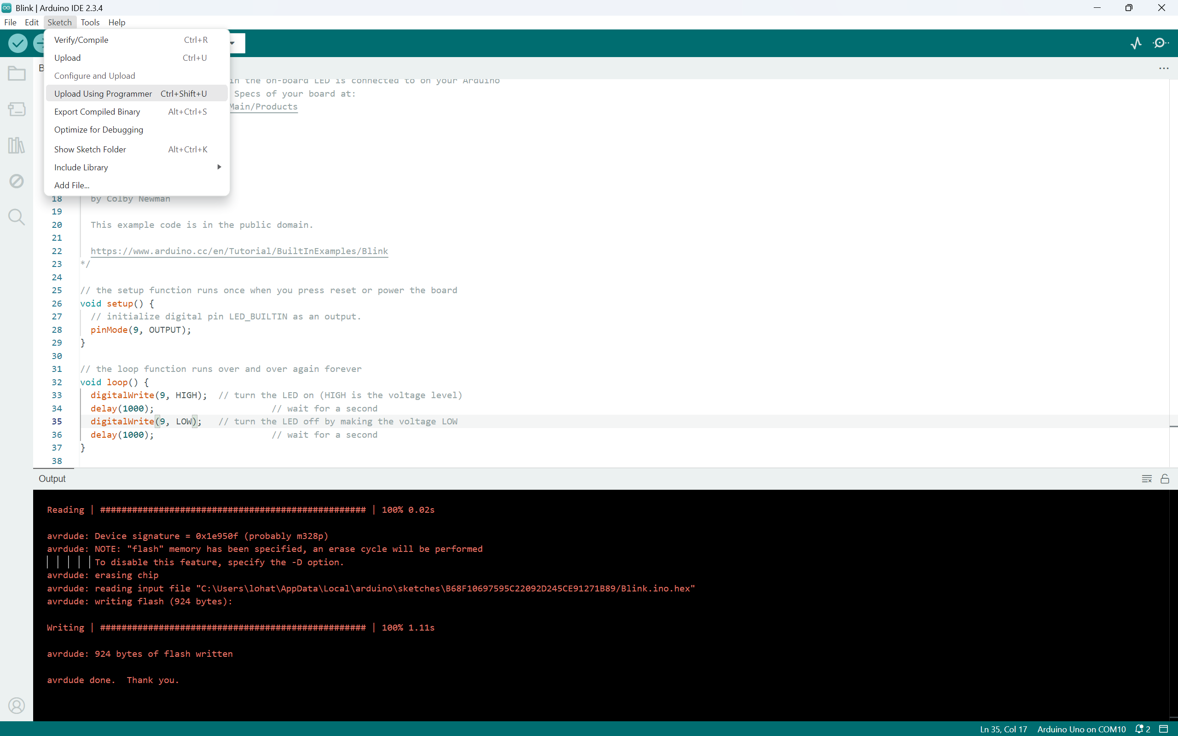
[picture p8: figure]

1) Upload Arduino as ISP to Arduino Uno
2) Connect Arduino to Atmega (RST, SCK, MISO, MOSI) -> (10, 13, 12 , 11)
3) New Sketch -> tools -> programmer = Arduino as isp
  a. Tools - > burn bootloader
4) Get normal sketch
5) Sketch -> upload using programmer

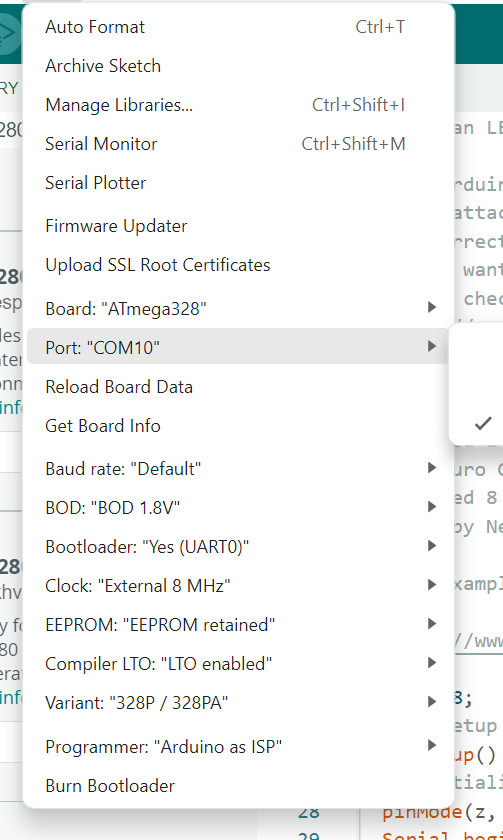
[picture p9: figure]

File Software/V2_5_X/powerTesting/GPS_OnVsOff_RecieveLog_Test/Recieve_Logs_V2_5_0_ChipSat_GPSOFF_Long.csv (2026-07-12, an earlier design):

Time | Counter (n) | Voltage (V) | SoC (%) | Temp (c)
15:08:46.017 | 25 | 3.83 | 40.1 | 29
15:08:55.044 | 27 | 3.82 | 40.1 | 29
15:08:59.557 | 28 | 3.82 | 40.1 | 29
15:09:04.068 | 29 | 3.82 | 40.1 | 30
15:09:08.580 | 30 | 3.82 | 40.1 | 30
15:09:13.093 | 31 | 3.83 | 40.1 | 30
15:09:17.602 | 32 | 3.82 | 40.1 | 30
15:09:22.112 | 33 | 3.82 | 40.1 | 30
15:09:26.625 | 34 | 3.82 | 40.1 | 30
15:09:31.173 | 35 | 3.82 | 40.1 | 30
15:09:35.642 | 36 | 3.82 | 40.1 | 30
15:09:40.177 | 37 | 3.83 | 40.1 | 30
15:09:44.667 | 38 | 3.82 | 40.1 | 31
15:09:49.207 | 39 | 3.82 | 40.1 | 31
15:09:53.680 | 40 | 3.83 | 40.1 | 31
15:09:58.201 | 41 | 3.82 | 40.1 | 31
15:10:02.699 | 42 | 3.82 | 40.1 | 31
15:10:07.206 | 43 | 3.82 | 40.1 | 31
15:10:11.714 | 44 | 3.82 | 40.1 | 31
15:10:16.225 | 45 | 3.82 | 40.1 | 31
15:10:20.735 | 46 | 3.81 | 40.1 | 31
15:10:25.236 | 47 | 3.82 | 40.1 | 31
15:10:29.745 | 48 | 3.82 | 40.1 | 32
15:10:34.256 | 49 | 3.82 | 40.1 | 31
15:10:38.763 | 50 | 3.82 | 40.1 | 31
15:10:43.270 | 51 | 3.82 | 40.1 | 31
15:10:47.779 | 52 | 3.82 | 40.1 | 31
15:10:52.283 | 53 | 3.82 | 40.1 | 32
15:10:56.789 | 54 | 3.82 | 40.1 | 32
15:11:01.297 | 55 | 3.82 | 40.1 | 31
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

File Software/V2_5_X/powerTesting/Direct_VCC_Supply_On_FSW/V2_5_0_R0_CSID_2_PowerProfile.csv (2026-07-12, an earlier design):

Time | Voltage | Current | Max Current
11:45:36.775 | 3316.25 | 25 | 36.25
11:45:36.776 | 3315 | 18.75 | 36.25
11:45:36.858 | 3313.75 | 25 | 36.25
11:45:36.957 | 3315 | 26.25 | 36.25
11:45:37.059 | 3316.25 | 25 | 36.25
11:45:37.161 | 3313.75 | 25 | 36.25
11:45:37.263 | 3312.5 | 20 | 36.25
11:45:37.364 | 3315 | 23.75 | 36.25
11:45:37.466 | 3313.75 | 26.25 | 36.25
11:45:37.568 | 3316.25 | 23.75 | 36.25
11:45:37.708 | 3315 | 23.75 | 36.25
11:45:37.805 | 3313.75 | 30 | 36.25
11:45:37.874 | 3316.25 | 35 | 36.25
11:45:37.976 | 3317.5 | 40 | 36.25
11:45:38.077 | 3316.25 | 27.5 | 40
11:45:38.179 | 3313.75 | 33.75 | 40
11:45:38.281 | 3313.75 | 30 | 40
11:45:38.382 | 3315 | 35 | 40
11:45:38.483 | 3316.25 | 32.5 | 40
11:45:38.586 | 3313.75 | 33.75 | 40
11:45:38.729 | 3313.75 | 32.5 | 40
11:45:38.790 | 3317.5 | 38.75 | 40
11:45:38.892 | 3316.25 | 38.75 | 40
11:45:38.993 | 3315 | 37.5 | 40
11:45:39.096 | 3315 | 36.25 | 40
11:45:39.197 | 3313.75 | 33.75 | 40
11:45:39.298 | 3313.75 | 37.5 | 40
11:45:39.400 | 3316.25 | 35 | 40
11:45:39.502 | 3313.75 | 38.75 | 40
11:45:39.604 | 3312.5 | 35 | 40
11:45:39.707 | 3313.75 | 33.75 | 40
11:45:39.807 | 3313.75 | 36.25 | 40
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

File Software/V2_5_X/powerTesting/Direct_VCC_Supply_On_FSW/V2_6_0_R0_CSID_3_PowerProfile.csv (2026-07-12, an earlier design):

Time | Voltage | Current | Max Current
11:36:53.906 | 3296.25 | 32.5 | 36.25
11:36:53.982 | 3295 | 37.5 | 36.25
11:36:54.084 | 3296.25 | 43.75 | 37.5
11:36:54.186 | 3291.25 | 50 | 43.75
11:36:54.287 | 3296.25 | 33.75 | 50
11:36:54.424 | 3293.75 | 38.75 | 50
11:36:54.491 | 3293.75 | 33.75 | 50
11:36:54.593 | 3295 | 41.25 | 50
11:36:54.695 | 3295 | 35 | 50
11:36:54.799 | 3293.75 | 36.25 | 50
11:36:54.899 | 3293.75 | 37.5 | 50
11:36:55.000 | 3293.75 | 35 | 50
11:36:55.102 | 3295 | 40 | 50
11:36:55.204 | 3292.5 | 33.75 | 50
11:36:55.306 | 3296.25 | 33.75 | 50
11:36:55.427 | 3295 | 35 | 50
11:36:55.837 | 3293.75 | 37.5 | 50
11:36:55.837 | 3293.75 | 37.5 | 50
11:36:55.837 | 3296.25 | 40 | 50
11:36:55.837 | 3296.25 | 36.25 | 50
11:36:55.917 | 3295 | 36.25 | 50
11:36:56.019 | 3291.25 | 40 | 50
11:36:56.120 | 3297.5 | 38.75 | 50
11:36:56.222 | 3296.25 | 37.5 | 50
11:36:56.324 | 3296.25 | 36.25 | 50
11:36:56.426 | 3295 | 35 | 50
11:36:56.527 | 3297.5 | 36.25 | 50
11:36:56.629 | 3293.75 | 43.75 | 50
11:36:56.731 | 3295 | 43.75 | 50
11:36:56.833 | 3292.5 | 43.75 | 50
11:36:56.935 | 3295 | 41.25 | 50
11:36:57.037 | 3295 | 40 | 50
11:36:57.138 | 3295 | 38.75 | 50
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

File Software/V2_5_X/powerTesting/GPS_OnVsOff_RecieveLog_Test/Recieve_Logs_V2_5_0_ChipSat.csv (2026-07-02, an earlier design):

Time | Counter (n) | Voltage (V) | SoC (%) | Temp (c)
18:39:33.506 | 1 | 3.99 | 75.9 | 26
18:39:38.137 | 2 | 3.99 | 75.9 | 26
18:39:42.764 | 3 | 3.99 | 75.9 | 26
18:39:47.383 | 4 | 3.98 | 75.9 | 25
18:39:52.002 | 5 | 3.98 | 75.9 | 25
18:39:56.618 | 6 | 3.98 | 75.9 | 25
18:40:01.226 | 7 | 3.98 | 75.9 | 25
18:40:05.834 | 8 | 3.98 | 75.9 | 25
18:40:10.442 | 9 | 3.98 | 75.9 | 25
18:40:15.041 | 10 | 3.98 | 75.9 | 25
18:40:19.641 | 11 | 3.98 | 75.9 | 24
18:40:24.241 | 12 | 3.98 | 75.9 | 24
18:40:28.841 | 13 | 3.98 | 75.9 | 24
18:40:33.433 | 14 | 3.98 | 75.9 | 24
18:40:38.028 | 15 | 3.98 | 75.9 | 24
18:40:42.623 | 16 | 3.98 | 75.9 | 24
18:40:47.216 | 17 | 3.98 | 75.9 | 24
18:40:51.806 | 18 | 3.98 | 75.9 | 24
18:40:56.397 | 19 | 3.97 | 75.9 | 24
18:41:01.002 | 20 | 3.97 | 75.9 | 24
18:41:05.574 | 21 | 3.97 | 75.9 | 24
18:41:10.161 | 22 | 3.97 | 75.9 | 24
18:41:14.748 | 23 | 3.98 | 75.9 | 24
18:41:19.335 | 24 | 3.97 | 75.7 | 24
18:41:23.918 | 25 | 3.97 | 75.7 | 24
18:41:28.503 | 26 | 3.97 | 75.7 | 24
18:41:33.088 | 27 | 3.97 | 75.7 | 24
18:41:37.667 | 28 | 3.97 | 75.7 | 24
18:41:42.247 | 29 | 3.97 | 75.7 | 24
18:41:46.830 | 30 | 3.97 | 75.7 | 24
18:41:51.412 | 31 | 3.97 | 75.7 | 24
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

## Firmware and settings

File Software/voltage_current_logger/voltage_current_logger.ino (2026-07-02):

#include <Adafruit_INA260.h>

Adafruit_INA260 ina260 = Adafruit_INA260();

void setup() {
  Serial.begin(115200);
  // Wait until serial port is opened
  while (!Serial) { delay(10); }

  Serial.println("Adafruit INA260 Test");

  if (!ina260.begin()) {
    Serial.println("Couldn't find INA260 chip");
    while (1);
  }
  Serial.println("Found INA260 chip");
}
float peak = 0;
float busV = 0;
float busI = 0;
void loop() {
  busV = ina260.readBusVoltage();
  if(busI>peak){
    peak = busI;
  }
  busI = ina260.readCurrent();
  Serial.println(String(busV)+','+String(busI)+","+String(peak));
  

  //Serial.println();
  delay(100);
}

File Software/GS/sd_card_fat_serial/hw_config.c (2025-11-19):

/* hw_config.c
Copyright 2021 Carl John Kugler III
FROM
https://github.com/carlk3/no-OS-FatFS-SD-SDIO-SPI-RPi-Pico/tree/main?tab=readme-ov-file

Licensed under the Apache License, Version 2.0 (the License); you may not use
this file except in compliance with the License. You may obtain a copy of the
License at

   http://www.apache.org/licenses/LICENSE-2.0
Unless required by applicable law or agreed to in writing, software distributed
under the License is distributed on an AS IS BASIS, WITHOUT WARRANTIES OR
CONDITIONS OF ANY KIND, either express or implied. See the License for the
specific language governing permissions and limitations under the License.
*/

/*
This file should be tailored to match the hardware design.

See
https://github.com/carlk3/no-OS-FatFS-SD-SDIO-SPI-RPi-Pico/tree/main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
*/

#include "hw_config.h"

// define pins to be used
#define SPI_PORT spi0
// issues having on same bus as LoRa
// #define SPI_MISO 4
// #define SPI_MOSI 3
// #define SPI_SCK 2
#define SPI_CS 5
#define SPI_MISO 0
#define SPI_MOSI 7
#define SPI_SCK 6

/* Configuration of hardware SPI object */
static spi_t spi = {
    .hw_inst = SPI_PORT,  // SPI component
    .sck_gpio = SPI_SCK,    // GPIO number (not Pico pin number)
    .mosi_gpio = SPI_MOSI,
    .miso_gpio = SPI_MISO,
    //.baud_rate = 125 * 1000 * 1000 / 8  // 15625000 Hz
    //.baud_rate = 125 * 1000 * 1000 / 6  // 20833333 Hz
    .baud_rate = 30000000  //125 * 1000 * 1000 / 4  // 31250000 Hz
    //.baud_rate = 125 * 1000 * 1000 / 2  // 62500000 Hz
};

/* SPI Interface */
static sd_spi_if_t spi_if = {
    .spi = &spi,  // Pointer to the SPI driving this card
    .ss_gpio = SPI_CS // 7  // The SPI slave select GPIO for this SD card
};

/* Configuration of the SD Card socket object */
static sd_card_t sd_card = {
    .type = SD_IF_SPI,
    .spi_if_p = &spi_if  // Pointer to the SPI interface driving this card
};

/* ********************************************************************** */

size_t sd_get_num() { return 1; }

/**
 * @brief Get a pointer to an SD card object by its number.
 *
 * @param[in] num The number of the SD card to get.
 *
 * @return A pointer to the SD card object, or @c NULL if the number is invalid.
 */
sd_card_t *sd_get_by_num(size_t num) {
    if (0 == num) {
        // The number 0 is a valid SD card number.
        // Return a pointer to the sd_card object.
        return &sd_card;
    } else {
        // The number is invalid. Return @c NULL.
        return NULL;
    }
}

/* [] END OF FILE */

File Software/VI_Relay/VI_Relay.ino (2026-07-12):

#include <Adafruit_INA260.h>

#define DEBUG false

#define relay1Switch 2
#define relay2Switch 3
#define relay3Switch 4

#define relay1Addr 0x40
#define relay2Addr 0x41
#define relay3Addr 0x45

Adafruit_INA260 relay1INA = Adafruit_INA260();
Adafruit_INA260 relay2INA = Adafruit_INA260();
Adafruit_INA260 relay3INA = Adafruit_INA260();

float ina1BusV = 0;
float ina2BusV = 0;
float ina3BusV = 0;
float ina1Curr = 0;
float ina2Curr = 0;
float ina3Curr = 0;

unsigned long lastINARead = 0;

const int RELAY_ON = HIGH;
const int RELAY_OFF = LOW;

bool relay1State = false;
bool relay2State = false;
bool relay3State = false;

char serialBuffer[32];
byte serialIndex = 0;

void setup() {
  Serial.begin(115200);
  while (!Serial) { delay(10); }

  pinMode(relay1Switch, OUTPUT);
  pinMode(relay2Switch, OUTPUT);
  pinMode(relay3Switch, OUTPUT);

  applyRelayStates();

  if (!relay1INA.begin(relay1Addr)) {
    Serial.println("Couldn't find INA260 chip 1");
    while (1);
  }

  if (!relay2INA.begin(relay2Addr)) {
    Serial.println("Couldn't find INA260 chip 2");
    while (1);
  }

  if (!relay3INA.begin(relay3Addr)) {
    Serial.println("Couldn't find INA260 chip 3");
    while (1);
  }

  Serial.println("Enter 1, 2, 3, or combinations like 1,2 to toggle relays.");
  Serial.println("Enter 0 to turn all relays off.");
}

void loop() {
  handleSerialInput();

  if (millis() - lastINARead >= 250) {
    lastINARead = millis();

    readINAData(relay1INA, ina1BusV, ina1Curr);
    readINAData(relay2INA, ina2BusV, ina2Curr);
    readINAData(relay3INA, ina3BusV, ina3Curr);

    printINAData();
  }
}

void readINAData(Adafruit_INA260 &ina, float &busV, float &current) {
  busV = ina.readBusVoltage();
  current = ina.readCurrent();
}

void printINAData() {
  Serial.print(String(ina1BusV) + " , " + String(ina1Curr) + " , ");
  Serial.print(String(ina2BusV) + " , " + String(ina2Curr) + " , ");
  Serial.println(String(ina3BusV) + " , " + String(ina3Curr));
}

void applyRelayStates() {
  digitalWrite(relay1Switch, relay1State ? RELAY_ON : RELAY_OFF);
  digitalWrite(relay2Switch, relay2State ? RELAY_ON : RELAY_OFF);
  digitalWrite(relay3Switch, relay3State ? RELAY_ON : RELAY_OFF);
}

void handleSerialInput() {
  while (Serial.available() > 0) {
    char c = Serial.read();

    if (c == '\n' || c == '\r') {
      if (serialIndex > 0) {
        serialBuffer[serialIndex] = '\0';
        processRelayCommand(serialBuffer);
        serialIndex = 0;
      }
    } else {
      if (serialIndex < sizeof(serialBuffer) - 1) {
        serialBuffer[serialIndex++] = c;
      }
    }
  }
}

void processRelayCommand(char *cmd) {
  bool toggleRelay1 = false;
  bool toggleRelay2 = false;
  bool toggleRelay3 = false;
  bool turnAllOff = false;

  for (int i = 0; cmd[i] != '\0'; i++) {
    if (cmd[i] == '1') toggleRelay1 = true;
    if (cmd[i] == '2') toggleRelay2 = true;
    if (cmd[i] == '3') toggleRelay3 = true;
    if (cmd[i] == '0') turnAllOff = true;
  }

  if (turnAllOff) {
    relay1State = false;
    relay2State = false;
    relay3State = false;
  } else {
    if (toggleRelay1) relay1State = !relay1State;
    if (toggleRelay2) relay2State = !relay2State;
    if (toggleRelay3) relay3State = !relay3State;
  }

  applyRelayStates();

  if (DEBUG){
    Serial.print("Relays enabled: ");
    if (relay1State) Serial.print("1 ");
    if (relay2State) Serial.print("2 ");
    if (relay3State) Serial.print("3 ");
    if (!relay1State && !relay2State && !relay3State) Serial.print("none");
    Serial.println();
  }
}

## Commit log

2025-10-30 fixed redefinition error for print_tx_rx by creating separate Constants.cpp file. LoRaRadio::setTCX0: changed bool return type to void. outputs as expected.
2025-12-03 Fixed SD card writing for ground station
    [receive.cpp]
2025-12-10 pushed gs pico code, doesn't work with current spreading factor
    [receive.cpp]
2025-12-11 updated imu to include gyro, gps now record alt not bme
2026-01-28 Delete Hardware/2025 CAD directory
    uploading new version
    [.75in PC082-1100-7750-MW-3000-CG-N-IN.ipt, 15205A117_Spring Hinge.ipt, 15205A214_Opening Spring Hinge.ipt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]
2026-01-28 Create 2025 CAD
2026-01-28 Create CAD 1-18
2026-01-28 Update CAD 1-18
2026-02-06 [TESTED] updated imu, things are printing in serial
2026-02-09 updated values for imu init (probably need to change later)
2026-02-23 Revert "updated values for imu init (probably need to change later)"
    This reverts commit d5c4f6f1ff1f470982e00727d7c659fece22fb81.
    retesting old version to see if it works better
2026-02-23 changed enable(x) to 50, added new checks for gryo/linaccel/mag
    values seem reasonable now
    - magnitude takes awhile to calibrate
    - imu values don't all update at the same time (e.g. some repeat values for linAccel when gyro updates)
2026-03-06 [TESTED-ish] serialize() and deserialize() work tentatively
    also fixed scaling for imu values
    -> was debugging stuff for that, was reinitializing a lot, added consecutiveFailures counter
2026-03-24 duty cycle implementation
    not yet power tested
2026-04-28 fixed libary for IMU
    [power_profile_BOHR.csv]
